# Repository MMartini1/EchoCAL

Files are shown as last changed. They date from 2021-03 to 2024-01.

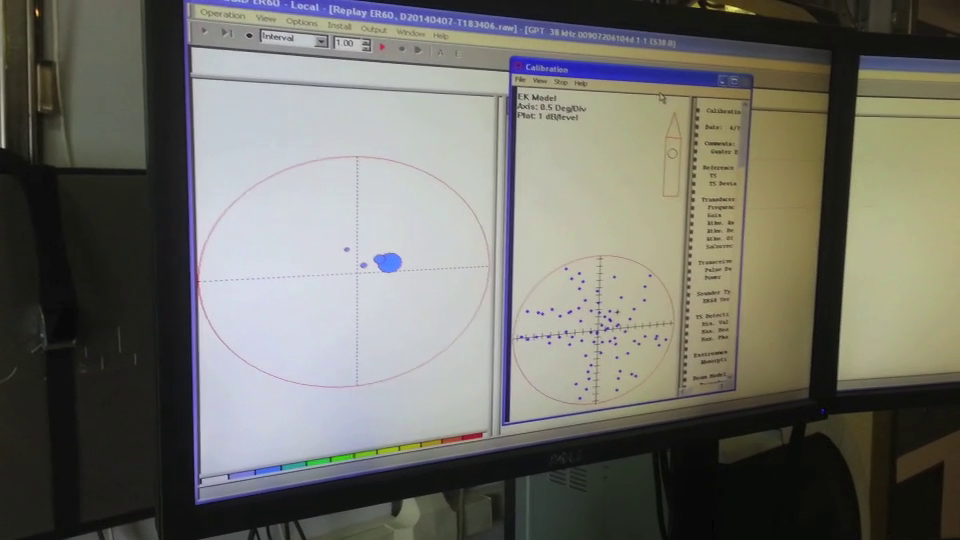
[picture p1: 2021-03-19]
Documentation/WGFAST_Presentation/CalSphere3.png

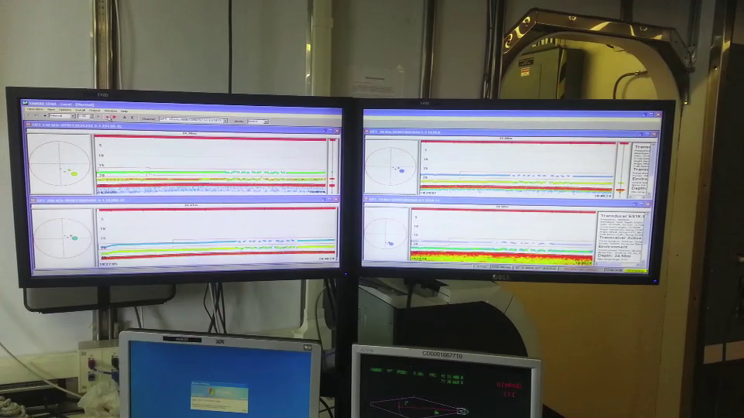
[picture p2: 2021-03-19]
Documentation/WGFAST_Presentation/AutoNav_Primarydisplay.png

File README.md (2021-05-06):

# EchoCAL: A Wireless Echosounder Calibration System. EchoCAL Logo

The EchoCAL Wireless Echosounder Calibration System was designed to give Ocean Acoustics researchers the ability to control motorized downriggers remotely during scientific echosounder calibrations. A typical downrigger station consists of a control box wired to a Canon downrigger which is mounted on the railing of the research vessel. A typical calibration on a research vessel requires at least three downrigger stations. (Two on one side of the vessel, and one on the other side.)

Smaller Picture of Downrigger Station

The reseacher can control these downriggers wirelessly from inside the vessel. (See the figure below for a system diagram.)

Diagram of EchoCAL System

## EchoCAL Project Files:

The following folders contain the required documentation to build one EchoCAL system:

### DesignFiles:

This folder contains a parts list as well as wiring diagrams for all EchoCAL hardware. This folder has two subfolders, "CircuitCard" and "WiringDiagrams". The "CircuitCard" folder contains the design files to manufacture the EchoCAL custom printed circuitboard (PCB). The "WiringDiagram" folder contains CAD, DXF, and PDF drawings for building all of the hardware for EchoCAL.

### Documentation:

This folder has the latest documentation.

### EchoCAL_GUI_Source:

This folder contains all of the [Netbeans](https://netbeans.org) JAVA Project source code for the EchoCAL Graphical User Interface (GUI).

### Parallax_Firmware:

This folder contains the firmware for the [Parallax Propeller](https://www.parallax.com/catalog/microcontrollers/propeller) Microcontroller.

### WGFAST_Presentation:

This folder contains a Microsoft PowerPoint presentation of the EchoCAL System. This presentation was given at the Working Group on Fisheries Acoustics, Science, and Technology ([WGFAST](http://www.ices.dk/community/groups/Pages/WGFAST.aspx)) meeting in May 2014. 

### bin:

This folder contains the executable code for the EchoCAL Graphical User Interface (GUI). The JAVA executable code is stored as a ZIP archive that can be downloaded and extracted on a user's computer. The archive was created using Netbeans IDE 8.1 and JAVA JDK 1.8 (64bit).

The "bin" folder has two subfolders, "Win64" and "Linux64". Download the proper version depending on which operating system you will be using.

## Designers:

* **Joseph Godlewski** - *Hardware/Firmware Design* - [jmgodlewski](https://github.com/jmgodlewski)

* **Michael Ryan**     - *EchoCAL GUI Design* - [spacetimeengineer](https://github.com/spacetimeengineer)

* **Marinna Martini**  - *EchoCAL Maintenance* - [MMartini1](https://github.com/MMartini1)

## License

EchoCAL is open source! See [LICENSE](./LICENSE.md) for complete license information.

The hardware/software design was written as beerware; if you see us at the local pub, and you've found the hardware and software helpful, please buy us a round!

Please use, reuse, and modify these files as you see fit. Please maintain attribution to NOAA Fisheries, Northeast Fisheries Science Center, and release anything derivative under the same license.

Distributed as-is; no warranty is given.

This project is licensed under the MIT License - see the [LICENSE.md](LICENSE.md) file for details.

## Acknowledgments:

* [Fizzed.com](http://fizzed.com/oss/rxtx-for-java) : Thanks to the developers at Fizzed.com for creating the open source 64-bit modules of the **RXTX** serial communication libraries for JAVA.

* [JInput](https://github.com/jinput/jinput) : Thanks to the developers and maintainers of the open source **JInput** JAVA module for interfacing USB Joystick controllers with Java applications.

* [Parallax Object Exchange](http://obex.parallax.com/) : Thanks to all of the developers who supplied numerous SPIN and Assembly code for the **Parallax Propeller** microcontroller. Their work has made the Propeller microcontroller a joy to work with.

This repository is a scientific product and is not official communication of the National Oceanic and Atmospheric Administration, or the United States Department of Commerce. All NOAA GitHub project code is provided on an ‘as is’ basis and the user assumes responsibility for its use. Any claims against the Department of Commerce or Department of Commerce bureaus stemming from the use of this GitHub project will be governed by all applicable Federal law. Any reference to specific commercial products, processes, or services by service mark, trademark, manufacturer, or otherwise, does not constitute or imply their endorsement, recommendation or favoring by the Department of Commerce. The Department of Commerce seal and logo, or the seal and logo of a DOC bureau, shall not be used in any manner to imply endorsement of any commercial product or activity by DOC or the United States Government.

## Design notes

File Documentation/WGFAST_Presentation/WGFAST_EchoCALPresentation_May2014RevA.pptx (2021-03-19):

## EchoCAL: A mobile wireless calibration system for echo sounders.

Presented By:
Joseph M. Godlewski and Michael Ryan
NOAA,NMFS, NEFSC
Ecosystems Survey Branch
Advanced Sampling Technologies

## EchoCAL: A mobile wireless calibration system for echo sounders

- EchoCAL Hardware:
  - System Diagram;
  - Control Box Assembly;
  - Microcontroller Firmware;
  - Zigbee Wireless Protocol;
    - Wireless Base Station.
    - Wireless Routers.
- EchoCAL Software GUI.
- Results.

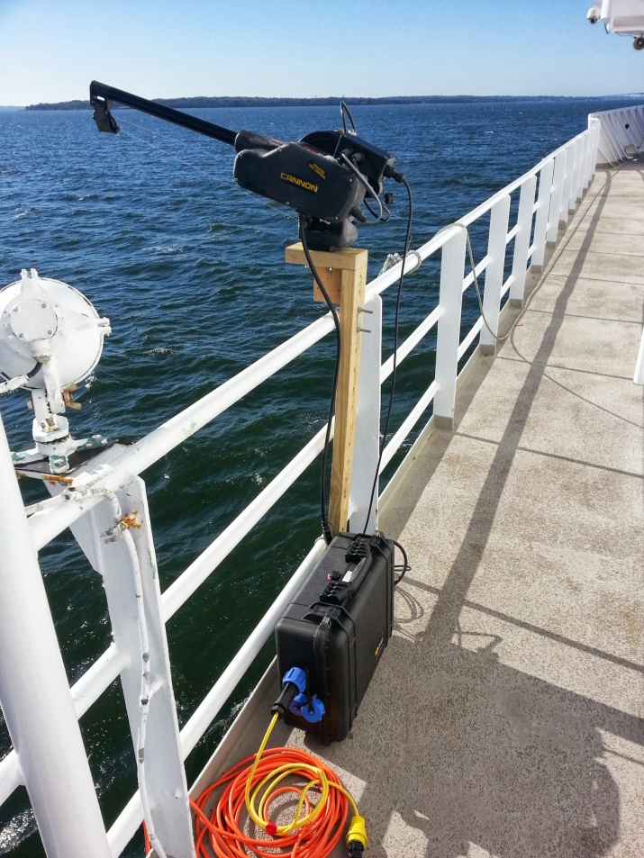
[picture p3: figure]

## EchoCAL System Diagram:

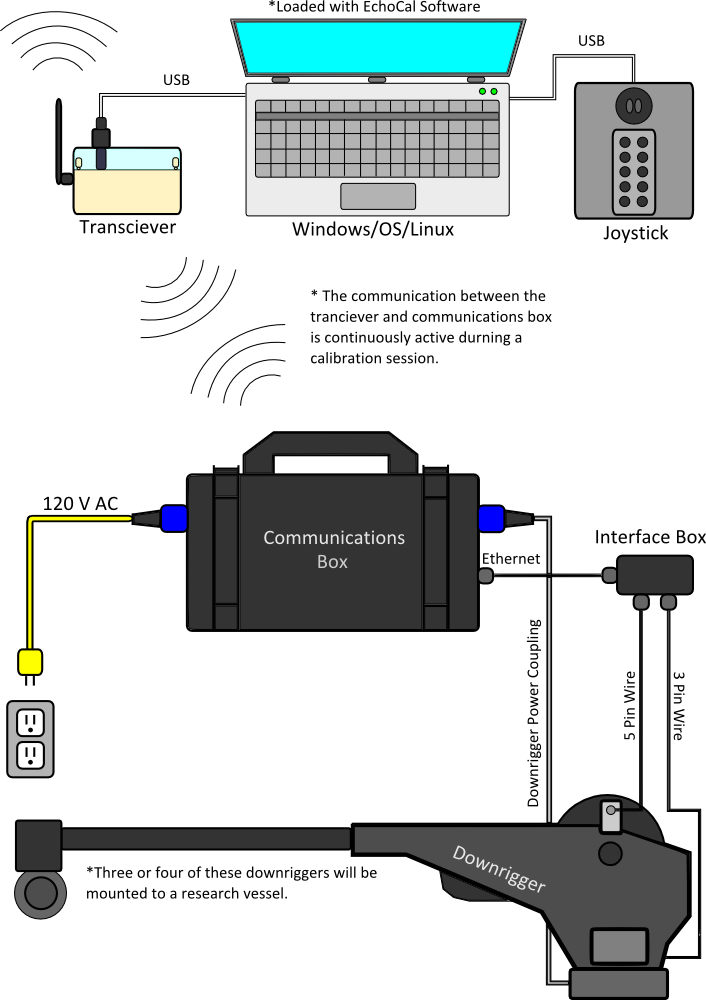
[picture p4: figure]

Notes: Modifications to Cannon Downrigger:

Added connector to downrigger case to wire control box relays in parallel with switch in downrigger.
Mounted 3PS Inc. Quadrature Encoder to outside of downrigger case.
Two magnets installed on downrigger wheel, each mounted at 180 degrees apart.
(This gives us approximately 6 inches of line movement with every “COUNT” of the encoder.)

## EchoCAL Control Box Assembly:

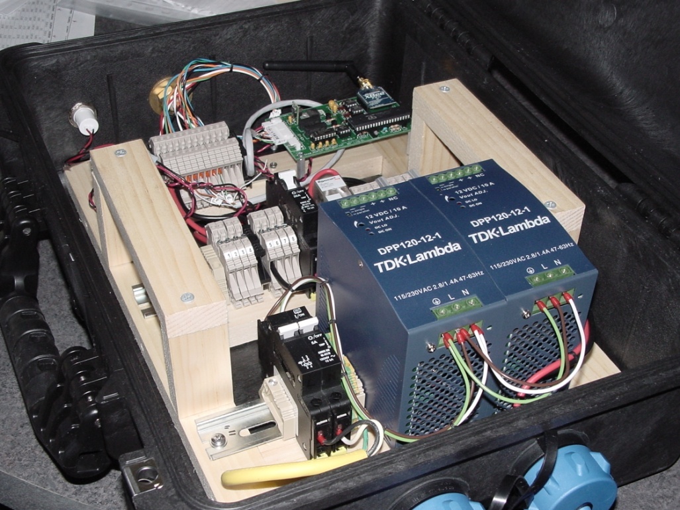
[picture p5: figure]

- Control Box consists of the following components:
  - Two TDK Lambda 12VDC, 10 Amp Power supplies;
  - One TDK Lambda 12VDC, 830 mA Power supply;
  - Custom circuit board with Parallax microcontroller and Digi International XBee Pro Wireless Transceiver;
  - Two power relays for switching between battery and AC power modes.

## Parallax Microcontroller Firmware:

- Parallax Microcontroller programmed using two languages designed specifically for it:
  - “Spin” language = High-level object-based,
  - “Propeller Assembly” = Low-level, highly optimized.
- Microcontroller has eight processing cores (Cogs) which act as a hardware threading mechanism. Allows functions to run in parallel. EchoCAL firmware uses three processing Cogs:
  - One Cog for Main program.
  - Second Cog for handling data and command I/O with XBee Pro transceiver.
  - Third Cog for monitoring the Encoder output and determining direction and line length (ie. Counts) that the downrigger has accomplished.

## XBee Pro Base Station and Router:

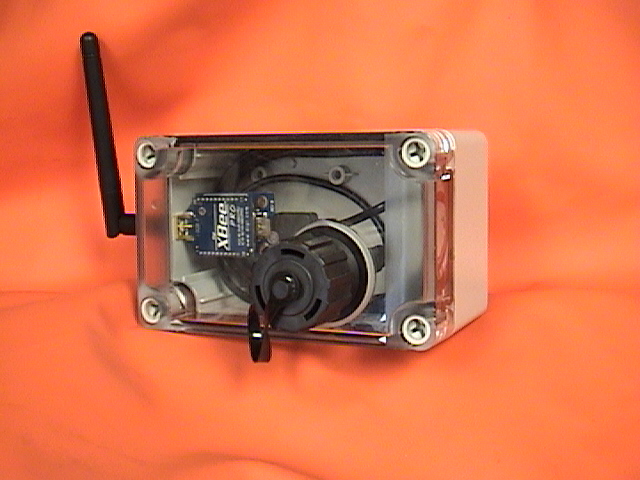
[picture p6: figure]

- The XBee Pro Base Station consists of the following:
  - Parallax XBee USB Adapter board;
  - One Digi Inc. XBee Pro Wireless Transceiver;
  - Power provided by USB bus in the PC.
- The XBee Pro Router hardware:
  - Powered by a 12 VDC, 2000 mAh battery pack.
  - Custom PCB which converts 12 VDC to 3.6 VDC for XBee Pro transceiver operation.

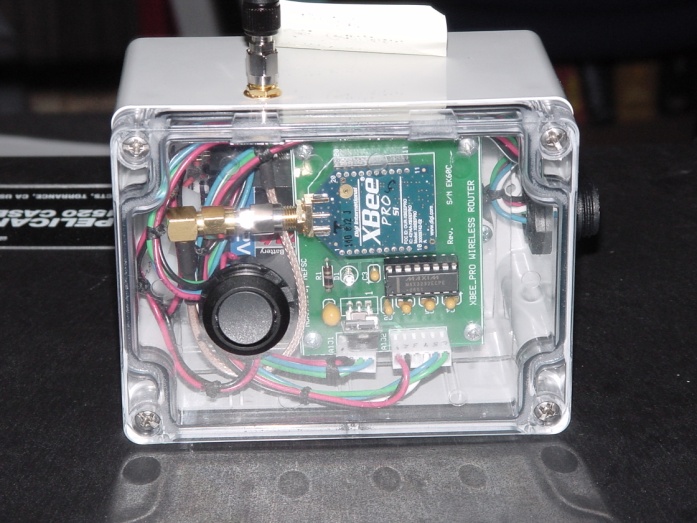
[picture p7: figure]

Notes: XBee Pro Base Station:
- Parallax XBee USB adapter board eliminates the need to build a custom circuit board.
- Simply mount XBee Pro transceiver to adapter board and you are in business.
- Power provided through the USB bus.

XBee Pro Router:
- Powered by a 12 VDC 2000 mAh battery pack.
- Custom circuit board that converts 12 VDC to 3.6 VDC for use with the XBee Pro transceiver.
- Board also contains an Analog Devices ADM3202 RS232 transceiver chip to provide RS232 support for upgrading the XBee Pro transceiver.
- We can do away with the custom PCB if we use the same Parallax XBee USB adapter board that was used in the Base Station.

## XBee Pro Digimesh Network:

- The XBee Pro network is known as a Low Rate Wireless Personal Area Network (LR-WPAN), commonly referred to as a Wireless Sensor Network:
  - Incorporates an Ad Hoc On-Demand Distance Vector mesh routing;
  - Self-healing and discovery capable for network stability;
  - Operates in the 2.4 GHz wireless frequency band;

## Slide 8

EchoCAL Software Interface:

- EchoCAL Software:
  - Developed using JAVA NetBeans IDE platform;
  - Joystick enabled;
  - Location indicators;
  - Programmatic sensors,
  - Hardware safety functions,
  - Automatic navigation function,
  - Navigate function (Sphere locator function).

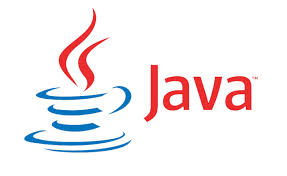
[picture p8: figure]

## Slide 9

EchoCAL Geometry Manager Inputs:
(Visual Reference)

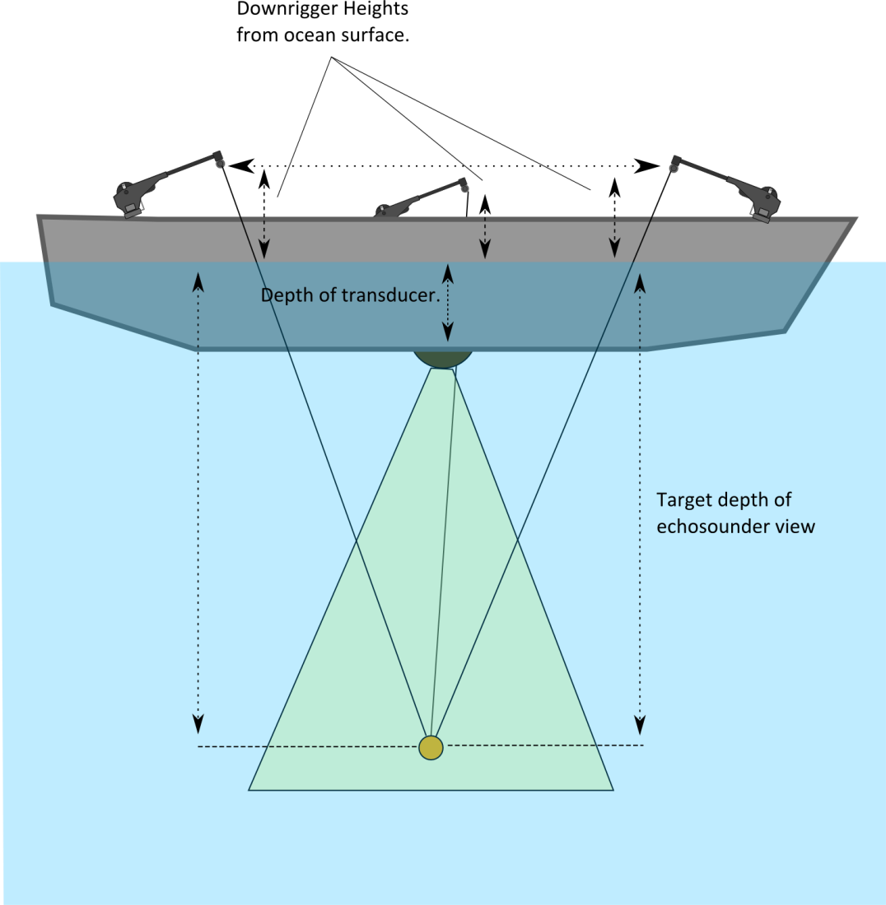
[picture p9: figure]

- Measurements are used to build a geometrical reference map which allows the EchoCAL system to perform accurate automated calibration sessions.

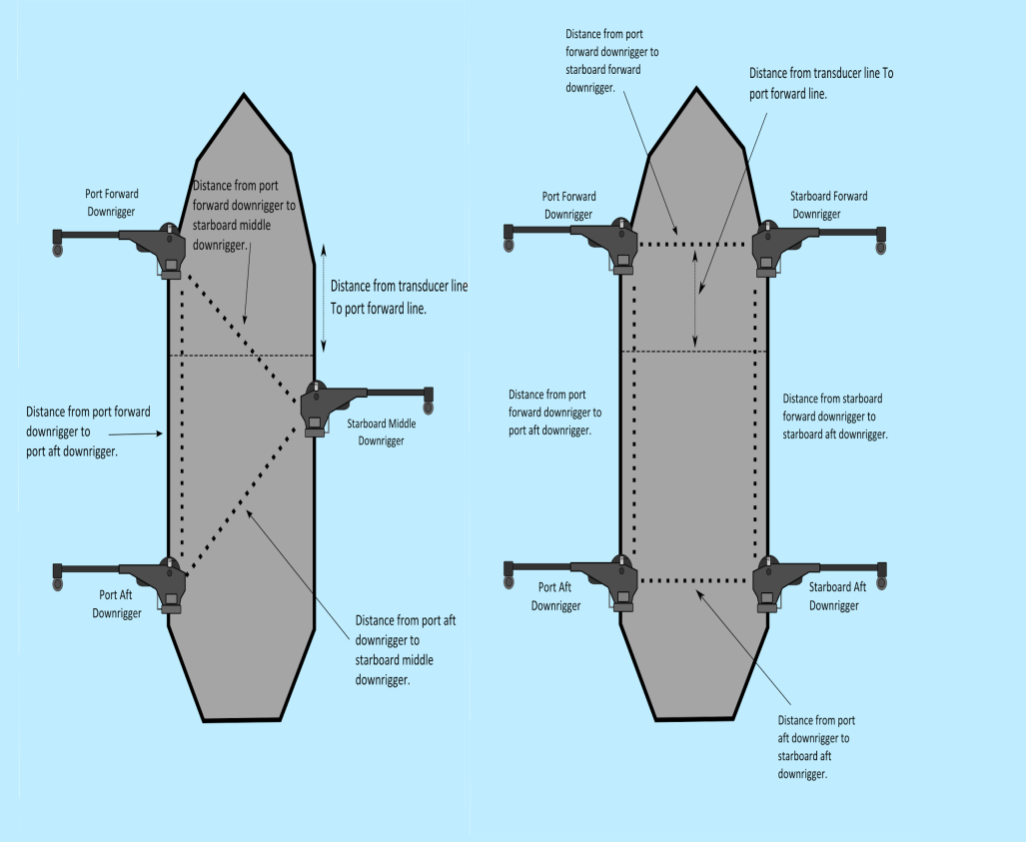
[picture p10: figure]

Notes: Vessel Config file is used to provide a general location of the mounted downriggers on the vessel.
Vessel specific measurements are made to determine the location of the downriggers with respect to the onboard echosounder transducers.

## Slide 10

EchoCAL Graphical User Interface:

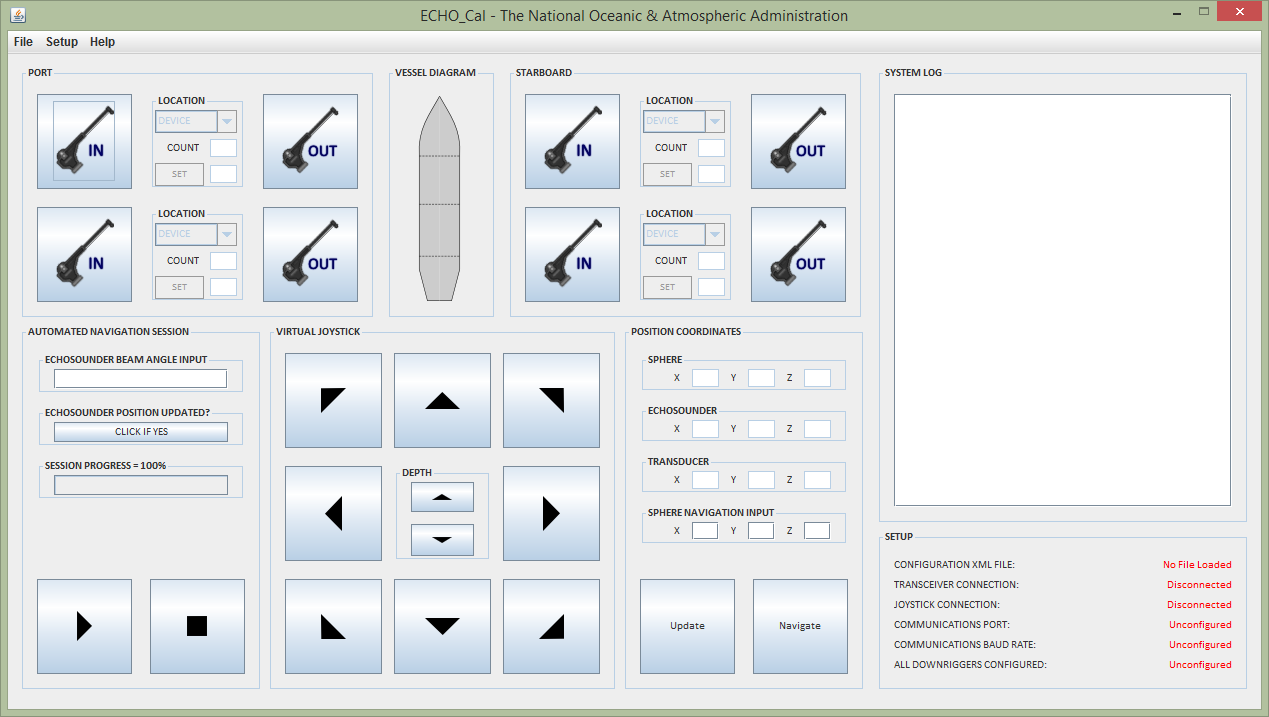
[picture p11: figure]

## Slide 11

EchoCAL’s True Power:
Coordinate Transformation Algorithms

- EchoCAL Software Coordinate Solutions:
  - Uses a process of coordinate filtering to find the Euclidian position of the calibration sphere.
  - Runs on a separate thread so that the geometrical information is updated in real time.
  - Uses the XML configuration file for a geometrical basis.
  - All inputs and outputs are Euclidian, but all calculations are done in downrigger coordinates.

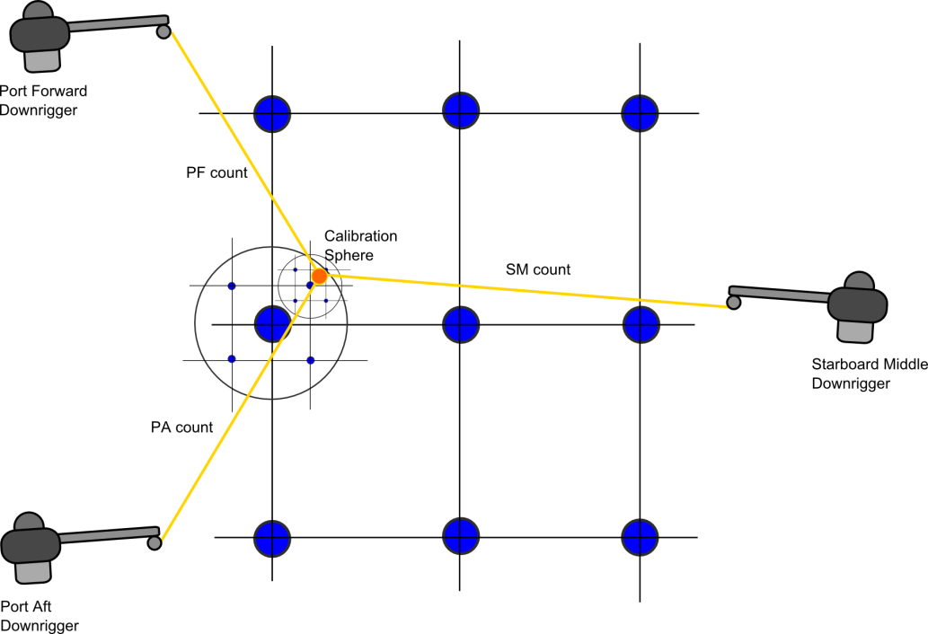
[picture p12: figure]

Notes: Graphic represents a two dimensional view of a three dimensional space.
Each circle represents a set of coordinates. The software checks which downrigger coord transformation is closest to the systems current downrigger counts, and builds another set of points around it. This method builds an array of coordinates

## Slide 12

EchoCAL Automated Calibration Session:

- EchoCALs Automated Navigation Function:
  - Automatically moves the sphere through echosounder beam in a “Star” shaped pattern.
  - Area covered is slightly larger than the beam angle that was input in the GUI.
  - Reasonable coverage is obtained in the echosounder beam.
  - An automated session takes approximately 10 minutes to perform, depending on beam angle size.

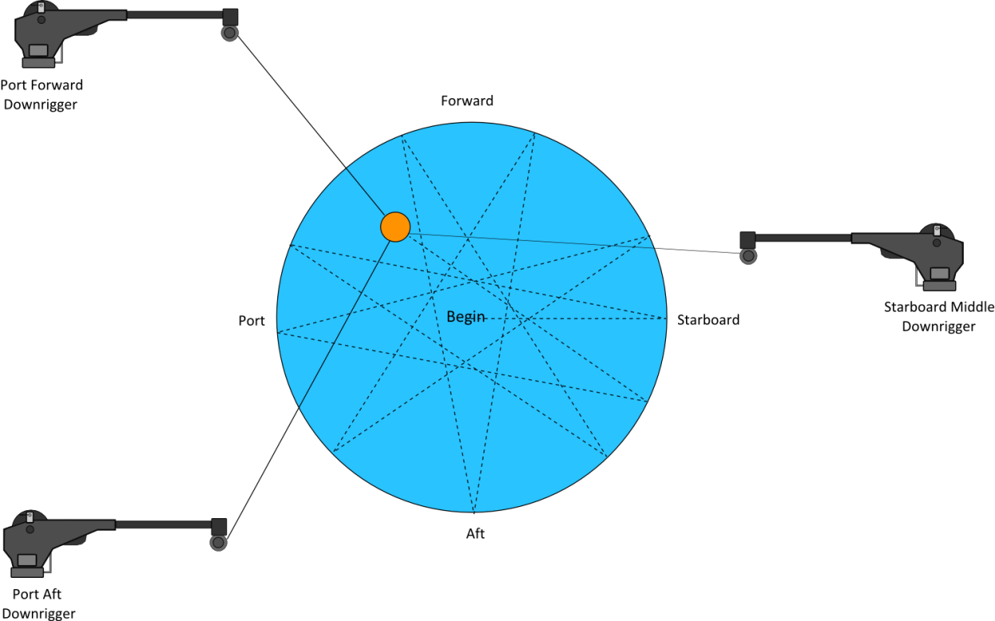
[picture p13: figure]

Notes: EchoCALs Automated Navigation Function:
Automatically moves the sphere through the echosounder beam in a “Star-shaped” pattern.
- Other patterns are being researched.
The area covered is slightly larger than the beam angle that was input in the GUI.
Reasonable coverage is obtained in the echosounder beam.
An automated session takes approximately 10 minutes to perform, depending on the beam angle size.

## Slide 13

EchoCAL Automated Calibration Session:

- EchoCALs Time Saving Abilities:
  - Initially locating the sphere in the echosounder beam can be a difficult task. (Especially when surface winds, or ocean currents are high.) Use of both the “Navigation” and “Auto-navigation” functions allow the operator to easily position the sphere in the echosounder’s beam.
  - Echosounder position updates; (Allows higher order corrections to geometry if system generated values are wrong).
  - Automated calibration sessions: Enjoy a coffee rather than standing out in the rain!

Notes: Time Saving Abilities:
- Initially finding the sphere in the echosounder beam can be a difficult task. (Especially when surface winds, or ocean currents are high.)
The “Navigation” and “Auto-navigation” functions of the EchoCAL software allow the operator to easily position the sphere in the echosounder’s
beam. The Navigation function will get the sphere to the proper depth, and in the vicinity of the echosounder’s beam. If the sphere is not seen
at this point, the operator can perform an initial “Auto-navigation” session with a larger than normal beam angle, and once the sphere appears
in the beam, the operator can stop the “Auto-navigation” session, and position the sphere using the joystick controls.
- Software allows the operator to update the position of the sphere in the center of a beam. This allows operator to reposition the sphere automatically in
the beam should the sphere somehow get lost during calibrations.

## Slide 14

Hardware Safety Functions:

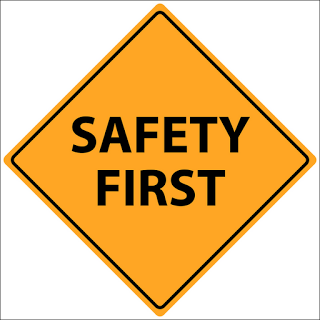
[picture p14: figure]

- EchoCAL Hardware Safety Functions:
  - Built-in tension sensor function to keep lines from breaking.
  - Built-in communication loss warning message.
  - Automatic system halting functions. (Pauses system when mechanical or communication failures occur).
  - Built-In real-time System Log for general information and system status.

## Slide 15

EchoCAL System Results:

- The EchoCAL echosounder calibration system has been used successfully on three NOAA vessels to date:
  - NOAA Ship Okeanos Explorer (April 2013),
  - NOAA Ship Gordon Gunter (April 2014),
  - NOAA Ship Henry Bigelow (September 2013, April 2014).
- Extending the wireless signal outside the vessels proved to be easier than expected. (Only three routers required for the above vessels.)

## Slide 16

EchoCAL System Results:


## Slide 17

EchoCAL System Results:

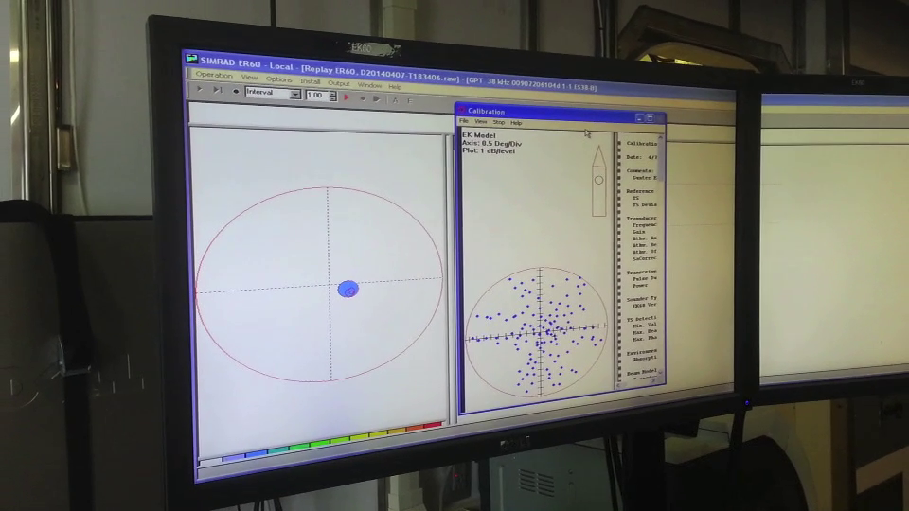
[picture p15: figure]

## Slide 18

- Questions?

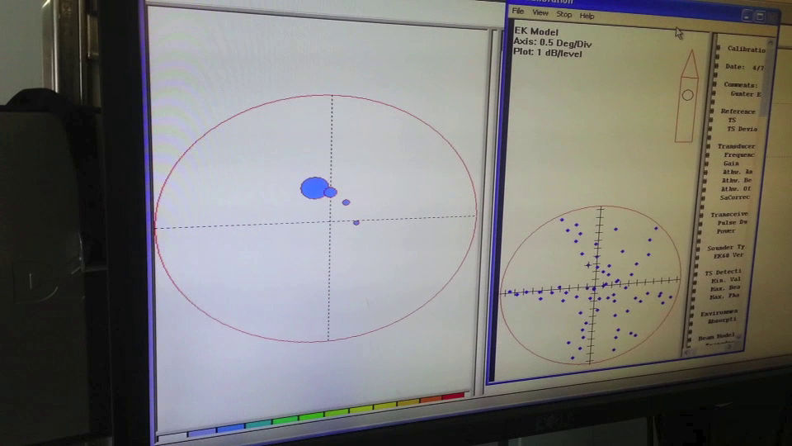
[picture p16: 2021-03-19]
Documentation/WGFAST_Presentation/CalSphere2.png

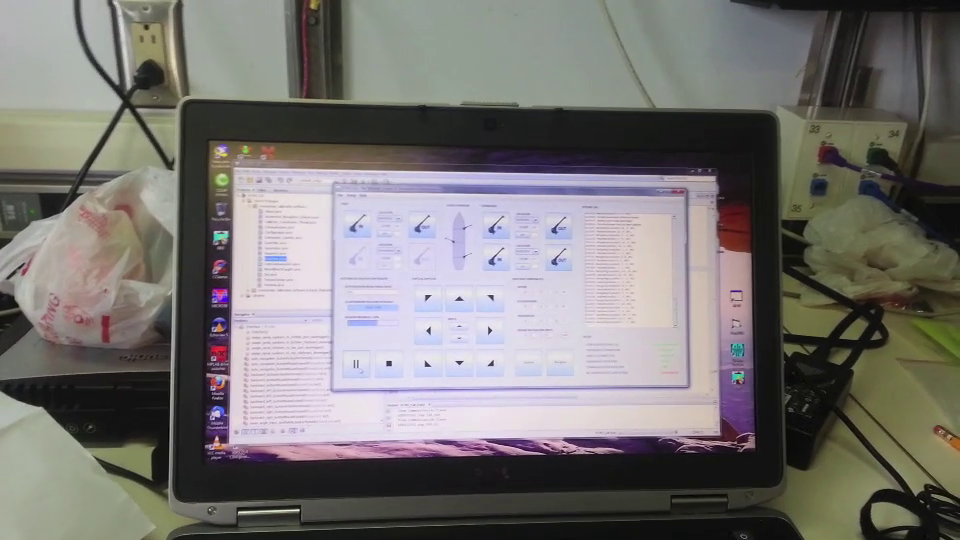
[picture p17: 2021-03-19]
Documentation/WGFAST_Presentation/EchoCAL_GUI.png

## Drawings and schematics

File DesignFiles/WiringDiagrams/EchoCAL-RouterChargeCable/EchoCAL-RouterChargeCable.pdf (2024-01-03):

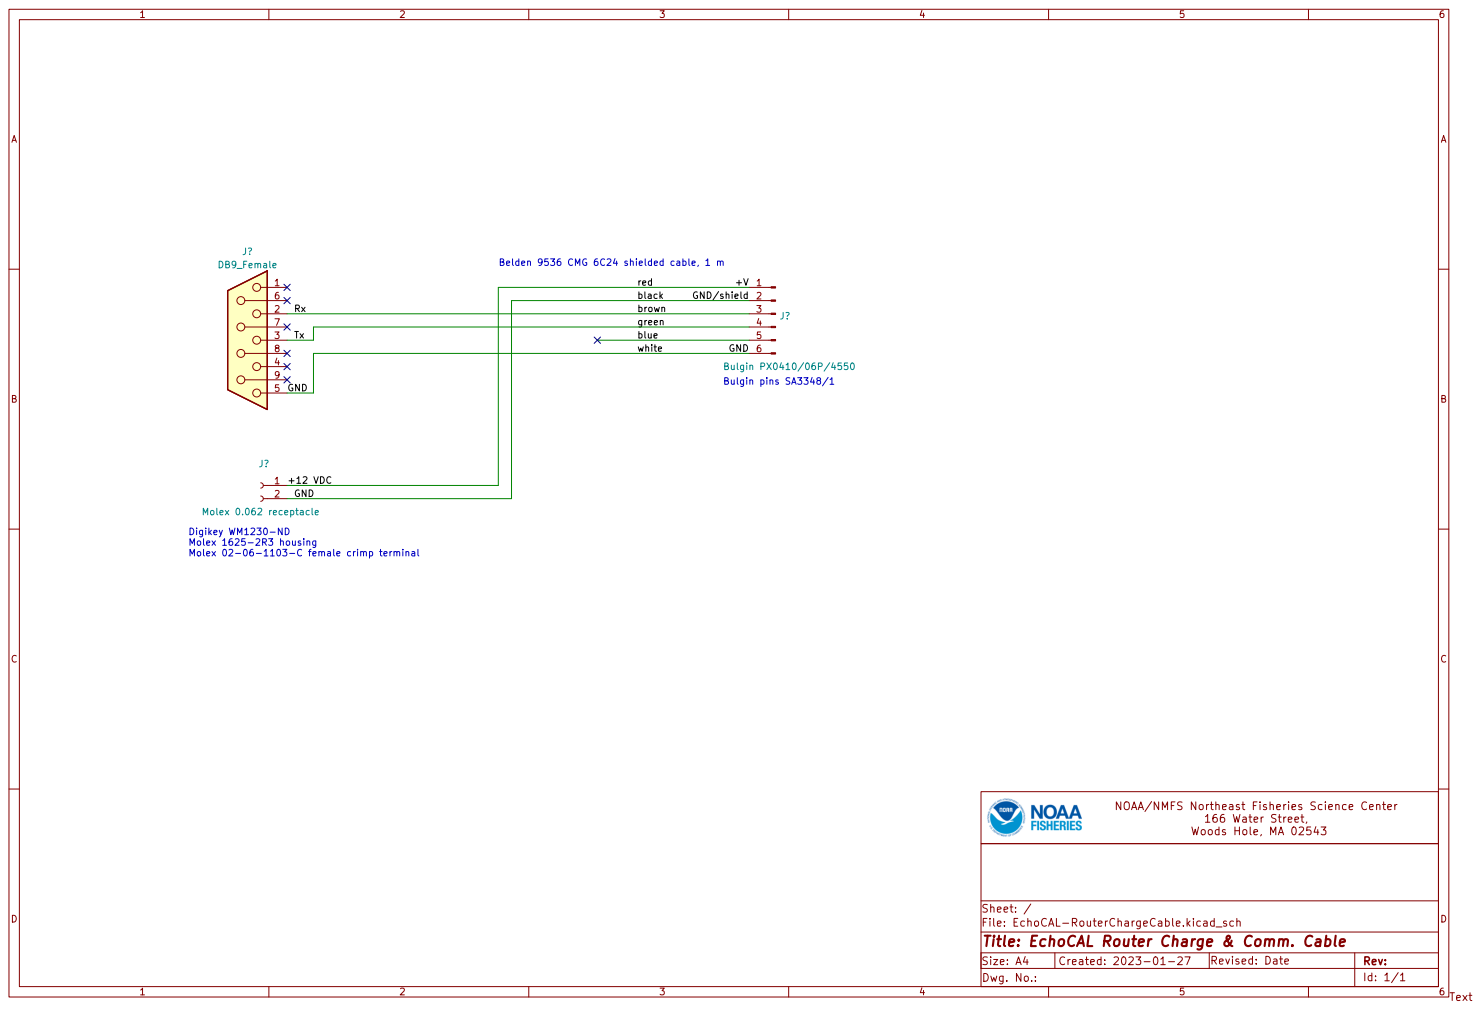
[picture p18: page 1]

Bulgin pins SA3348/1 Belden 9536 CMG 6C24 shielded cable, 1 m

Molex 1625-2R3 housing
Molex 02-06-1103-C female crimp terminal

File: EchoCAL-RouterChargeCable.kicad_sch Sheet: / NOAA/NMFS Northeast Fisheries Science Center

Id: 1/1 Title: EchoCAL Router Charge & Comm. Cable

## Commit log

2022-03-02 Troubleshooting and operational tips added by Mike Jech based on the Spring 2022 calibration of the NOAA ship Henry Bigelow.
2022-12-08 add schematic that was missing for this cable
    [EchoCAL-RouterChargeCable.kicad_pcb, EchoCAL-RouterChargeCable.kicad_sch]
2024-01-03 documentation update
    [EchoCAL-RouterChargeCable.kicad_sch]
